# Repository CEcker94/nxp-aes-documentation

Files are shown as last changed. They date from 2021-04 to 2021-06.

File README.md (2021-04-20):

# NXP-AES-Documentation (nxp-aes-documentation)
The documentation for a Project of three Master Engineering-Students at the university of applied sciences in Landshut Germany (Ambrosch Markus, Summer Matthias and Ecker Christian).

This repository contains all the datasheets, pictures, circuit diagrams and most importantly the report of this project.

### 1.1 Information
The goal of the project is the construction and programming of a model vehicle for the Next Experience (NXP) Cup with a specially built, self-driving vehicle. In this competition the 1:18 scale vehicles must drive safely and independently through a course in the shortest possible time. The roadway is bordered by two black stripes applied to a white background. The vehicle must recognize these limitations and, based on their evaluation, adjust the speed of the vehicle and its steering angle.

### 1.2 Project
For the Project [>click-here<](https://github.com/CEcker94/nxp-aes-proj) 

The project contains the c-code for the autonomous driving vehicle.

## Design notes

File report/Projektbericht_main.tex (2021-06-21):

%*********************************************************************
%*************************** Main Document ***************************
%*********************************************************************

% Header includes document class and packages
\input{header/header}

\begin{document}

\pagenumbering{Alph} % Intern werden die Ersten seiten mit Alpha-Stiel nummeriert um Doppelreferenzen zu vermeiden 

% Titlepage
\input{titlepage/titlepage}
%%FERTIG

% Set page counter to 2 and page numbering to Roman
\pagenumbering{Roman}
\setcounter{page}{2}

% Section 0 Vorwort und Projektlinks
\input{sec0/sec0}
%%FERTIG

% Table of contents
\input{inserts/toc/toc}

% Table of acronyms
\input{inserts/acronym/acronym}

% Saving page counter value for attachement
\newcounter{pagecountersaving}
\setcounter{pagecountersaving}{\value{page}}

% Set page counter to 1 and page numbering to arabic
\pagenumbering{arabic}
\setcounter{page}{1}

% Section 1 Einführung
\input{sec1/sec1}
%FERTIG

% Section 2 Aufbau des Fahrzeugs
\input{sec2/sec2}
%FERTIG

% Section 3 Controllerplatine und Programmiertool
\input{sec3/sec3}
%FERTIG

% Section 4 Antrieb des Fahrzeugs
\input{sec4/sec4}
%FERTIG

% Section 5 Lenkung des Fahrzeugs
\input{sec5/sec5}
%FERTIG

% Section 6 Bedienungs-Board
\input{sec6/sec6}
%%FERTIG

% Section 7 Streckenerkennung des Fahrzeugs
\input{sec7/sec7}
%%FERTIG

% Section 8 Verteilerplatine
\input{sec8/sec8}
%%FERTIG

% Section 9 Regelung
%\input{sec9/sec9}

% Section 10 Inbetriebnahme des Fahrzeugs
%\input{sec10/sec10}

% Section 11 Zusammenfassung, Fazit und Ausblick
\input{sec11/sec11}
%--------------------------------------------------------------------Kapitel muss noch geschrieben werden

\pagenumbering{Roman}
\setcounter{page} {\thepagecountersaving}

% Table of graphics
\input{inserts/graphics/graphics}
%%FERTIG

% Table of sources
\input{inserts/sources/sources}
%%FERTIG

% Attachements
\input{attachement/attachement}
%---------------------------------------------------------------------Schaltplan einfügen
%---------------------------------------------------------------------Verweise auf Anhang in Text nicht vergessen!

\end{document}

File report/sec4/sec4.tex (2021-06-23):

%*****************************************************************
%*************************** Section 4 ***************************
%********************* Antrieb des Fahrzeugs *********************
%*****************************************************************

\pagestyle{fancy}
\rhead{\thepage} \chead{} \lhead{\ref{Sec4}. \nameref{Sec4}}
\cfoot{}

\section{Antrieb des Fahrzeugs}\label{Sec4}

Wie in Kapitel \ref{Sec2Sub1} beschrieben, wird das Fahrzeug von zwei \acp{BLDCMot} angetrieben, die im Folgenden genauer erklärt werden. Zusätzlich dazu wird in diesem Kapitel auch näher auf die Montage der Antriebskomponenten, die Programmierung des Antriebsbausteins, die Konfiguration der Motorcontroller und die Drehzahlmessung eingegangen.

\subsection{BLDC-Antrieb und Motorcontroller}\label{Sec4Sub1}

\acp{BLDCMot} sind im Wesentlichen wie permanent erregte Synchronmaschinen aufgebaut. Sie besitzen Magnete im Rotor und Einzelzahnwicklungen im Stator. Da solche Motoren häufig im \ac{RC}-Bereich Einsatz finden, gibt es zu deren Ansteuerung bereits vorgefertigte Bausteine, sogenannte \ac{ESC}. Diese haben zwei Signalpins für ein \ac{PWM}-Signal und zwei Anschlüsse zur Spannungsversorgung des Motorcontrollers, aus welchen die drei Strangspannungen für die Phasen des Antriebs generiert werden. Aus diesen Strangspannungen kann im übrigen auch die Motordrehzahl ermittelt werden, was im Rahmen dieser Projektarbeit auch eines der Ziele darstellt. An den Signalpins wird ein \ac{PWM}-Signal mit einer Frequenz von 50Hz angelegt, dessen Pulsbreite zwischen 1ms und 2ms liegen darf. Daraus resultiert ein Tastgrad zwischen 5\% (Stillstand) und 10\% (maximal erreichbare Drehzahl). Die maximale Drehzahl des Antriebs hängt von der Spannung des Akkus ab. Je geringer diese Spannung ist, desto geringer ist die maximal erreichbare Drehzahl. Der Anschluss der Motoren erfolgt nach der in Abbildung \ref{fig:SkizzeAntrieb} gezeigten Weise.

\begin{figure}[H] %H für Positionierung hier
 
\centering
\captionsetup{width=.95\textwidth}
\caption[Skizze zur Beschaltung eines \ac{ESC}s und \ac{BLDCMot}s]{Skizze zur Beschaltung eines \ac{ESC}s und \ac{BLDCMot}s; Versorgungsspannung des \ac{ESC}s in rot und schwarz (Masse), \ac{PWM}-Signalleitungen in grau und schwarz (Masse) und Anschlussleitungen des \ac{BLDCMot}s in rot, gelb und schwarz}\centering
\label{fig:SkizzeAntrieb}
\end{figure}

\subsection{Montage der Antriebskomponenten}\label{Sec4Sub2}

Die Komponenten des Fahrzeugantriebs, welcher über zwei \acp{BLDCMot} realisiert ist, sind auf der unteren Fahrzeugebene montiert. Die Motoren selbst sind mit zwei Schrauben an der Karosserie befestigt. An der Welle der Motoren befindet sich je ein Zahnrad mit 13 Zähnen, welches ein weiteres Zahnrad mit 90 Zähnen antreibt, das an der Antriebswelle befestigt ist. Das heißt, dass sich die Reifen bei 6,923 Umdrehungen der Motorwelle genau einmal drehen.\vspace{11pt}

In Abbildung \ref{fig:MontageMotorUebersetzung} sind die montierten Komponenten des linken Antriebs abgebildet. Die Befestigungsschrauben der Motoren sind dabei in rot hervorgehoben, die Befestigungsschrauben des Zahnrads der Antriebswelle in blau und die Befestigung des Reifens in orange. Das Zahnrad der Motorwelle ist durch Erhitzen geweitet und auf die Welle aufgesetzt worden. Zur Sicherheit dient hier etwas Sekundenkleber dazu, dass sich das Zahnrad auf der Welle nicht durchdreht. Sekundenkleber ist hier völlig ausreichend, da aufgrund der Übersetzung nur 1/7 des auf die Reifen wirkenden Moments auf das Zahnrad der Motorwelle wirkt.

\begin{figure}[H] %H für Positionierung hier
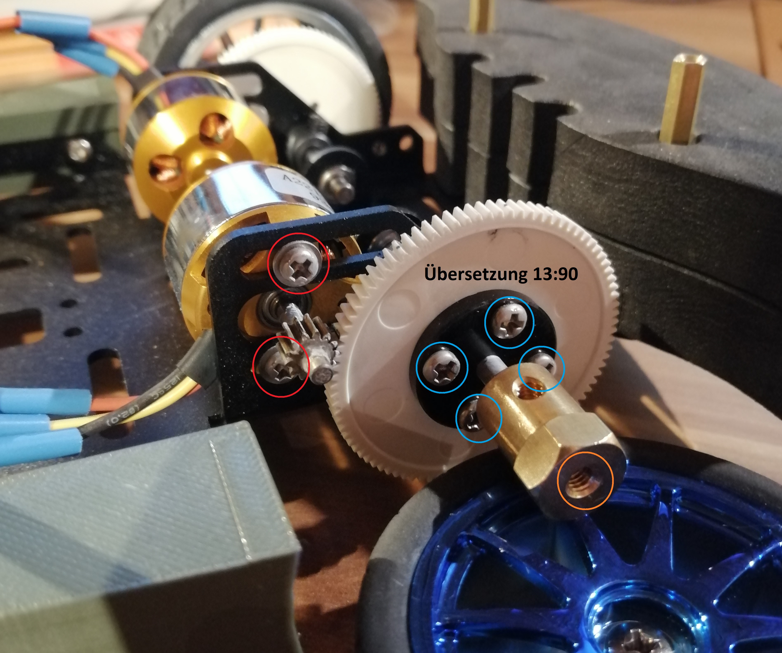
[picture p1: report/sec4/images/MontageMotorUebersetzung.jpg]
 
\centering
\captionsetup{width=.95\textwidth}
\caption[Montage der Antriebskomponenten]{Montage der \acp{BLDCMot} und Übersetzung auf die Antriebsachse; In rot die Befestigung des \ac{BLDCMot}s, in blau die Befestigung des Zahnrads an der Antriebswelle und in orange die Befestigung des Reifens}\centering
\label{fig:MontageMotorUebersetzung}
\end{figure}

\subsection{Konfiguration der Motorcontroller}\label{Sec4Sub3}

Die beiden Motorcontroller erwarten nach dem Zuschalten der Spannungsversorgung eine Initialisierungssequenz. Das Power-On-Ereignis wird vom \ac{ESC} mit drei Tönen (tief, mittel, hoch) signalisiert. Im Anschluss daran soll der Wert an der Signalleitung größer als 0\% sein. Das bedeutet, dass ein \ac{PWM}-Signal angelegt werden muss, welches eine Drehzahl N $\geq$ 0rpm repräsentiert. Der \ac{ESC} quittiert das Erkennen des \ac{PWM}-Signals mit einem tiefen Ton. Die Initialisierungssequenz ist allerdings erst dann beendet, wenn das \ac{PWM}-Signal an der Signalleitung zuerst vergrößert und dann auf 0\% verringert wird (N = 0rpm). Dabei gibt der \ac{ESC} einen letzten, hohen Ton von sich. Der Ablauf der Initialisierungssequenz ist in Abbildung \ref{fig:initESC} dargestellt. Nach dem letzten Ton ist die Initialisierung beendet und der \ac{BLDCMot} dreht sich in Abhängigkeit des an der Signalleitung anliegenden \ac{PWM}-Signals. 

\begin{figure}[H] %H für Positionierung hier
 
\centering
\captionsetup{width=.95\textwidth}
\caption[Initialisierungssequenz der \ac{ESC}s]{Initialisierungssequenz der \ac{ESC}s; Wert an der Signalleitung für die Initialisierungssequenz über der Zeit; 0\% entspricht dem \ac{PWM}-Tastgrad für den Stillstand und 100\% dem für die maximal erreichbare Drehzahl}\centering
\label{fig:initESC}
\end{figure}

Da die \ac{ESC}s individuell konfiguriert werden können und in der Dokumentation zu wenige Angaben gemacht werden, ist der Tastgrad für die Werte 0\% (Stillstand) und 100\% (maximal erreichbare Drehzahl) unbekannt. Deshalb ist es nicht möglich zu wissen, welche \ac{PWM}-Tastgrade für die Initialisierungssequenz verwendet werden müssen. Über die Konfiguration der \ac{ESC}s können die Grenzen für 0\% und 100\% selbst festgelegt werden. Für das Flashen der Motorcontroller wird die Software \glqq{}BLHeliSuite\grqq{} verwendet. Die Verbindung zwischen den \ac{ESC}s und der Software stellt ein Arduino Nano her.\vspace{11pt}

Der Arduino Nano muss zuvor mit einer neuen Software beschrieben werden. Um die \ac{ESC}s flashen zu können wird der Signalpin des zu programmierenden \ac{ESC} mit dem Pin D3 und der Massepin der Signalleitung mit einem Massepin des Arduino Nano verbunden. Danach wird in der Software \glqq{}BLHeliSuite\grqq{} im Reiter \glqq{}Make Interface\grqq{} eine neue Schnittstelle erstellt (siehe Abbildung \ref{fig:ConfigBLHeliSuite}). Auf der rechten Seite des Programm-Fensters wird ein Arduino Nano als Schnittstelle eingerichtet. Mit einem Klick auf den Button \glqq{}Arduino 4way-interface\grqq{} wird die neue Software, durch die die \ac{ESC}s neu konfiguriert werden können, auf den Arduino Nano geladen.

\begin{figure}[H] %H für Positionierung hier
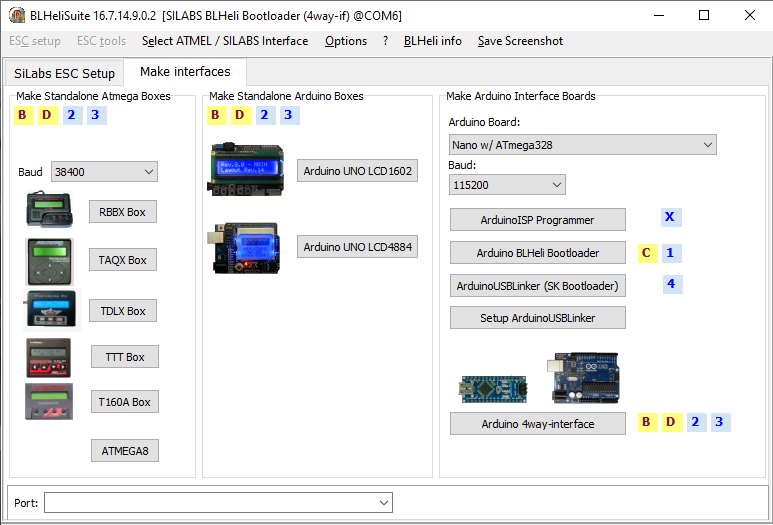
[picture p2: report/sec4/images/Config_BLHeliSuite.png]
 
\centering
\captionsetup{width=.95\textwidth}
\caption[Programmierung des Arduino Nano zur \ac{ESC}-Konfiguration]{Programmierung des Arduino Nano zur \ac{ESC}-Konfiguration mit der Software BLHeliSuite}\centering
\label{fig:ConfigBLHeliSuite}
\end{figure}

Nach dem Programmieren des Arduino Nano wird die Kommunikation der BLHeliSuite-Software mit dem \ac{ESC} hergestellt. Über die Schaltfläche \glqq{}Read Setup\grqq{} werden die voreingestellten Parameter des \ac{ESC} ausgelesen. Im nächsten Schritt werden die Zeiten für die Werte \glqq{}PPM min Throttle\grqq{} (0\% Aussteuergrad) und \glqq{}PPM max Throttle\grqq{} (100\% Aussteuergrad) auf 1100µs und 1900µs angepasst. Alle vorgenommenen Einstellungen sind in Abbildung \ref{fig:BLHeliSuite} einsehbar. Die Werte werden über die Betätigung der Schaltfläche \glqq{}Write Setup\grqq{} auf den \ac{ESC} geladen. Da jetzt die Werte für 0\% und 100\% Aussteuerung bekannt sind, können die einzelnen Schritte der Initialisierung im Programm des Fahrzeugs abgearbeitet werden.

\begin{figure}[H] %H für Positionierung hier
 
\centering
\captionsetup{width=.95\textwidth}
\caption[Parameter der neuen \ac{ESC}-Konfiguration]{Konfiguration der \ac{ESC}s mit der Software \glqq{}BLHeliSuite\grqq{}}\centering
\label{fig:BLHeliSuite}
\end{figure}

\subsection{Programmierung des Antriebsbausteins}\label{Sec4Sub4}

Der Antriebsbaustein der Software ist in zwei Dateien unterteilt, die Dateien \glqq{}drive.c\grqq{} und \glqq{}drive.h\grqq{}. Die Datei \glqq{}drive.h\grqq{} enthält alle relevanten Bibliotheken und Prototypen für die Datei \glqq{}drive.c\grqq{}.\vspace{11pt}

Außer der Einbindung der Bibliotheken und der Prototypen der Funktionen aus der Datei \glqq{}drive.c\grqq{} sind hier auch die Parameter für die Initialisierungssequenz der \ac{ESC}s und für die Initialisierung des Timers für die \ac{PWM}-Signale hinterlegt (Abbildung \ref{fig:DriveH}). 

\begin{figure}[H] %H für Positionierung hier
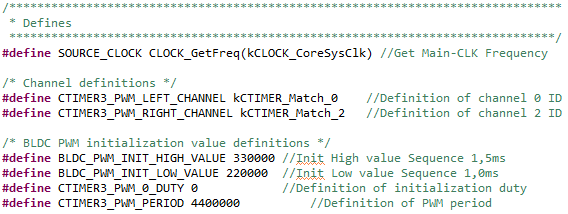
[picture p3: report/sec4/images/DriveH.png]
 
\centering
\captionsetup{width=.95\textwidth}
\caption[Relevante Zeilen der Datei \glqq{}drive.h\grqq{}]{Relevante Zeilen der Datei \glqq{}drive.h\grqq{} mit den Parametern für die Initialisierungssequenz der \ac{ESC}s und für die Initialisierung des \ac{PWM}-Timers}\centering
\label{fig:DriveH}
\end{figure}

Für die \ac{PWM}-Periodendauer wird bei der Initialisierung ein Wert von 4.400.000 Takten festgesetzt, woraus mit einer \ac{CPU}-Taktfrequenz von 220MHz (220.000.000 Takte pro Sekunde) eine Periodendauer von 20ms resultiert. Die Pulsbreite wird während des Programmablaufs regelmäßig überschrieben.\vspace{11pt}

Der \ac{ESC}-Initialisierungswert für den Stillstand (\glqq{}BLDC\_PWM\_INIT\_LOW\_VALUE\grqq{}, 220.000) entspricht hier einer \ac{PWM}-Pulsbreite von 1,0ms und der Initialisierungswert für die in etwa mittlere Aussteuerung (\glqq{}BLDC\_PWM\_INIT\_HIGH\_VALUE\grqq{}, 330.000) einer Breite von 1,5ms. Die volle Aussteuerung der Motoren wird, wie über die \glqq{}BLHeliSuite\grqq{} festgelegt, bei einer Pulsdauer von 1,9ms erreicht (BLDCMaxValue 1900µs, ca. 418.000). Eine Drehzahl von N = 0rpm wird theoretisch über die bei der \ac{ESC}-Konfiguration festgelegten 1,1ms ermöglicht (242.000). Da das \ac{PWM}-Signal leicht abweicht, wird ein etwas geringerer Wert veranlagt (BLDCMinValue 1090µs, ca. 240.000). Damit wird sichergestellt, dass sich die Räder im Stillstand nicht drehen.\vspace{11pt}

Die Parameter BLDCMaxValue und BLDCMinValue existieren im Code für die linke und rechte Antriebsseite separat (\glqq{}BLDCLeftMaxValue\grqq{}, \glqq{}BLDCLeftMinValue\grqq{} \& \glqq{}BLDCRightMaxValue\grqq{}, \glqq{}BLDCRightMinValue\grqq{}). Die Werte dieser Parameter kommen direkt aus dem \ac{EEPROM} und können mit dem Bedienungsboard eingestellt werden (siehe Abbildung \ref{fig:DriveC0}).\vspace{11pt}

\begin{figure}[H] %H für Positionierung hier
 
\centering
\captionsetup{width=.95\textwidth}
\caption[Extremwerte der Antriebsgeschwindigkeit als Parameter aus dem \ac{EEPROM}]{Extremwerte der Antriebsgeschwindigkeit als Parameter aus dem \ac{EEPROM}, deren Werte über das Bedienungsboard individuell einstellbar sind; Teil der Datei \glqq{}drive.c\grqq{}}\centering
\label{fig:DriveC0}
\end{figure}

\begin{figure}[H] %H für Positionierung hier
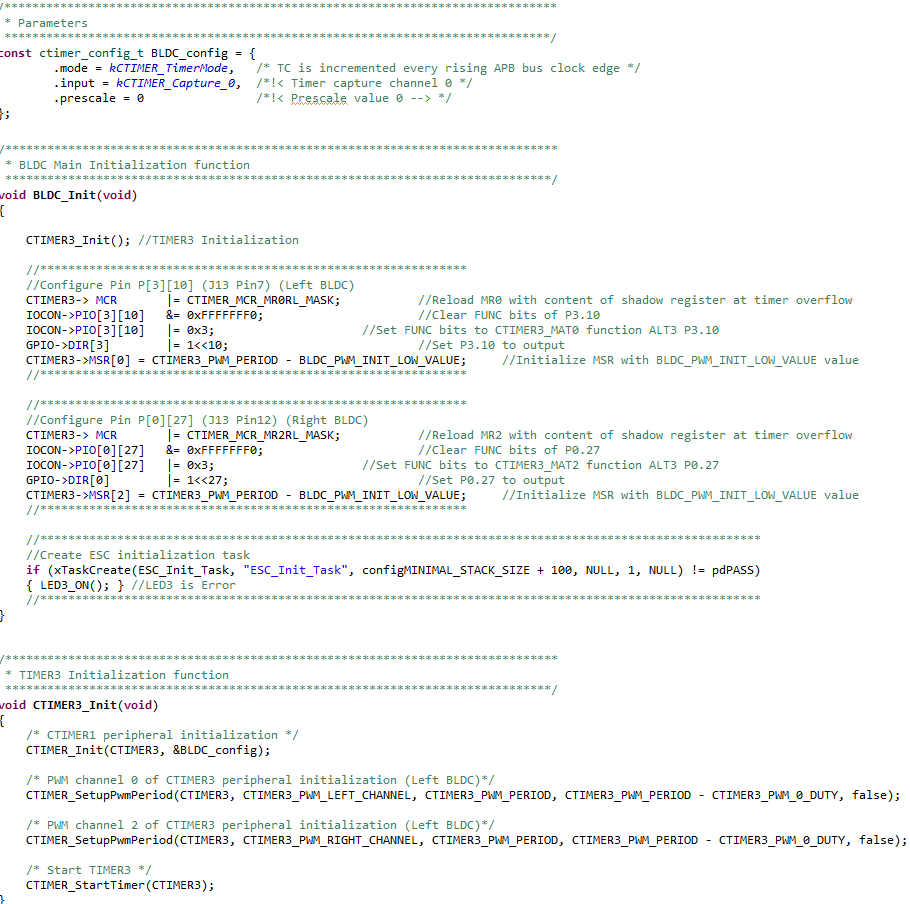
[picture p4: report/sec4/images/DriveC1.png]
 
\centering
\captionsetup{width=.95\textwidth}
\caption[Funktionen BLDC\_Init und CTIMER3\_Init der Datei \glqq{}drive.c\grqq{}]{Funktionen BLDC\_Init und CTIMER3\_Init der Datei \glqq{}drive.c\grqq{}}\centering
\label{fig:DriveC1}
\end{figure}

Auch die beiden \ac{PWM}-Timer (einer je Motorcontroller) benötigen bei der Initialisierung einige Parameter, deren Werte in der Datei \glqq{}drive.h\grqq{} festgelegt sind (PWM-Periodendauer, \ac{PWM}-Pulsdauer, Kanäle). Die Kanäle werden auf das Timer Match Register 2 (rechter Antrieb, \glqq{}kCTIMER\_Match\_2\grqq{}) und auf das Timer Match Register 0 (linker Antrieb, \glqq{}kCTIMER\_Match\_0\grqq{}) festgelegt, was bei dem verwendeten Controller den Pins P0.27 (rechts) und P3.10 (links) entspricht. Der Pin P3.10 wird auf der Controllerplatine über den Pin 7 und der Pin P0.27 über den Pin 12 der Buchsenleiste J13 nach außen geführt. Der Anschluss der Motorcontroller ist über den Anhang \glqq{}\nameref{SecAtt1}\grqq{} nachvollziehbar.\vspace{11pt}

Die Datei \glqq{}drive.c\grqq{} enthält die Funktionen zur Initialisierung der für die Verwendung der Antriebe notwendigen Controller-Peripherie (siehe Abbildung \ref{fig:DriveC1}) und zur Initialisierung der Motorcontroller (siehe Abbildung \ref{fig:DriveC2}).\vspace{11pt}

In der Funktion BLDC\_Init wird zuerst die Funktion CTIMER3\_Init aufgerufen, welche die beiden vorher festgelegten Kanäle des Timers C3 (\glqq{}kCTIMER\_Match\_0\grqq{} und \glqq{}kCTIMER\_Match\_2\grqq{}) mit den in der Datei ''drive.h'' festgelegten Parametern als \ac{PWM}-Timer mit einer Periodendauer von 20ms und einer Pulsdauer von 0ms initialisiert. Im Anschluss daran wird einzeln für beide Kanäle festgelegt, dass bei einem Timer-Überlauf die neuen Daten für die Pulslängen aus den Shadow-Registern geladen werden sollen. Zum Ändern der Geschwindigkeit eines der beiden Antriebe muss deshalb lediglich ein neuer Wert in das Shadow-Register geschrieben werden. Hier muss allerdings aufgepasst werden, da das Register nicht die Pulsbreite (On-Time) sondern die Off-Time erwartet. Deshalb muss der Wert, der eingetragen wird, der Periodendauer abzüglich der Pulsdauer entsprechen. Zusätzlich werden in der Funktion BLDC\_Init auch die Pins P3.10 und P0.27 für die Verwendung als \ac{PWM}-Ausgang des Timers C konfiguriert. Am Ende wird noch der erste \ac{ESC}-Initialisierungswert in die beiden Shadow-Register geschrieben, bevor die \ac{ESC}-Initialisierungsfunktion aufgerufen wird (siehe Abbildung \ref{fig:DriveC2}).\vspace{11pt}

Der Task BLDC\_Init\_Task beginnt mit dem Befüllen der Shadow-Register mit dem ersten Initialisierungswert. Nach einer Wartezeit von 2s wird der zweite Initialisierungswert in die Register geschrieben. Ebenfalls nach einer Zeit von 2s wird dann wieder der erste Initialisierungswert in die Shadow-Register geschrieben und die Initialisierung der \ac{ESC}s ist abgeschlossen. Die Wartezeiten sind notwendig, damit die \ac{ESC}s Zeit haben, die Änderungen zu erfassen.

\begin{figure}[H] %H für Positionierung hier
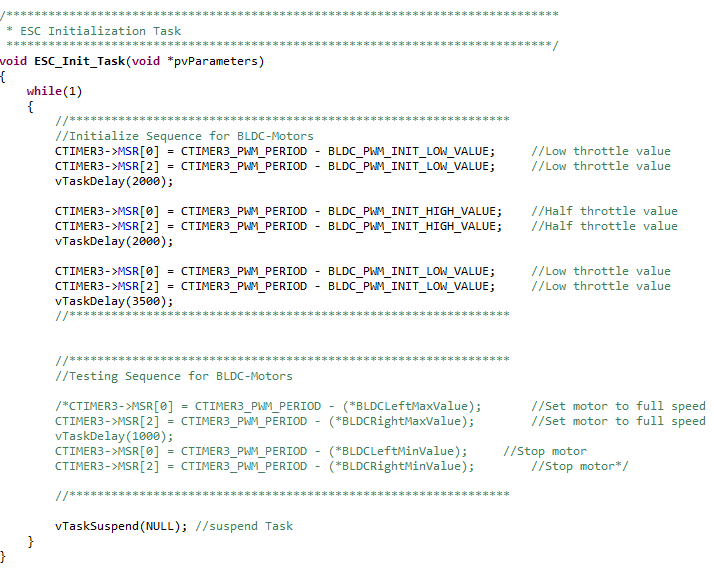
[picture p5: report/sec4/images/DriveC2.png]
 
\centering
\captionsetup{width=.95\textwidth}
\caption[Funktion BLDC\_Init\_Task der Datei \glqq{}drive.c\grqq{}]{Funktion BLDC\_Init\_Task der Datei \glqq{}drive.c\grqq{} zum Durchlaufen der Initialisierungssequenz der \ac{ESC}s}\centering
\label{fig:DriveC2}
\end{figure}

\newpage
\subsection{Drehzahlmessung}\label{Sec4Sub5}

Im folgenden Abschnitt zur Drehzahlmessung werden deren Notwendigkeit sowie Entwicklungsschritte und Realisierung erarbeitet. Des weiteren wird auch ein Ausblick für die Weiterentwicklung Schaltung gegeben.

\subsubsection{Erörterung der Notwendigkeit einer Drehzahlmessung}\label{Sec:NotwendigkeitDrehzahlmessung}

Die Quellspannung von Akkus verringert sich mit steigender Betriebszeit, weshalb bereits bei vorherigen Fahrzeug-Versionen eine Drehzahlmessung benötigt wird, um über eine Regelung die Spannungsabhängigkeit der Drehzahl bei \acp{DCMot} ausgleichen zu können. Die Spannungsabhängigkeit von \acp{DCMot} bereitet insbesondere beim Überfahren eines Hügels Probleme. Da die in den vorangegangenen Fahrzeugmodellen verwendeten \acp{DCMot} durch \acp{BLDCMot} ersetzt werden, stellt sich allerdings erneut die Frage nach der Notwendigkeit einer Drehzahlmessung. Die Variation der Drehzahl erfolgt bei \acp{DCMot} über die Änderung der Betriebsspannung, was auch die Abhängigkeit von der Versorgungsspannung erklärt. Die Drehzahlvariation bei einem \ac{BLDCMot} wird hingegen über eine Frequenzänderung der Strangspannungen realisiert. Zur Klärung der Frage nach einer Spannungsabhängigkeit der \acp{BLDCMot}, ist eine Messung am Prüfstand erforderlich.

\begin{figure}[H] %H für Positionierung hier
 
\centering
\captionsetup{width=.95\textwidth}
\caption[Messaufbau zur Prüfung der Spannungsabhängigkeit der \acp{BLDCMot}]{Messaufbau zur Prüfung der Spannungsabhängigkeit der \acp{BLDCMot}; in blau die Befestigung des Hecks an der Grundplatte des Prüfstands, in gelb die Befestigung der Vorderreifen am Prüfstand, in rot die DC-Motoren zur Spannungsmessung}\centering
\label{fig:Pruefstand01}
\end{figure}

Für die Durchführung der Messung wird ein bereits vorhandener Prüfstand für Modellfahrzeuge verwendet (siehe Abbildung \ref{fig:Pruefstand01}), welcher im Rahmen einer Bachelor-Abschlussarbeit an der HAW Landshut erstellt worden ist. Damit das Fahrzeug möglichst stabil auf dem Prüfstand steht und die Räder des Fahrzeugs ihre Rotationsbewegung besser auf die \acp{DCMot} des Prüfstands übertragen können, wird das Heck des Fahrzeugs mit Hilfe eines Drahtes am Prüfstand befestigt (Abbildung \ref{fig:Pruefstand01} blaue Markierung). Die vorderen Räder des Fahrzeuges sind ebenfalls am Prüfstand fixiert (Abbildung 44 gelbe Markierungen). \vspace{11pt}

Zur Überprüfung einer eventuellen Abhängigkeit der Drehzahl von der Versorgungsspannung, wird die Spannung an den vorhandenen \acp{DCMot} des Prüfstands gemessen, da diese direkt proportional zur Drehzahl ist (siehe Gleichung \ref{eq4.1}). Die Abhängigkeit der gemessenen Spannung von der Drehzahl ist allerdings nur annähernd linear, da die Drehmomentkonstante k\textsubscript{i} bei hohen Drehzahlen leicht einbricht. Aufgrund der für die Messung konstant eingestellten Pulsbreite von 1,5ms, spielt der Einbruch der Drehmomentkonstante allerdings keine große Rolle, da sich die Drehzahl, wenn überhaupt, nur sehr gering ändert. Dieser Zusammenhang kann deshalb vereinfachend als linear angenommen werden.\vspace{11pt}

Die Versorgungsspannung der \acp{ESC} wird für die Aufnahme verschiedener Messwerte zwischen 6,1V und 8V variiert. Ändert sich die gemessene Spannung mit der Variation der Versorgungsspannung, so ist das ein hinreichender Beweis dafür, dass die Drehzahl der \acp{BLDCMot} spannungsabhängig ist. Die Ergebnisse der Messreihe aus Tabelle \ref{tab:PruefstandMess01} sind zur einfacheren Auswertung in Abbildung \ref{fig:Pruefstand02} visualisiert.

\begin{equation}\label{eq4.1}
U_A = k_i \cdot N \cdot \frac{\pi}{30}
\end{equation}

\begin{table}[H]
\begin{tabular}{|c|c|c|c|c|c|c|c|c|c|c|}
\hline
\rule{0pt}{15pt} Messung & 1&2&3&4&5&6&7&8&9&10 \\
\hline
U\textsubscript{Versorgung} [$V$]&8.0&7.9&7.8&7.7&7.6&7.5&7.4&7.3&7.2&7.1 \\ 
\hline
U\textsubscript{Messung} [$V$]&5.80&5.75&5.65&5.57&5.48&5.40&5.35&5.25&5.18&5.09 \\
\hline
\hline
\rule{0pt}{15pt} Messung & 11&12&13&14&15&16&17&18&19&20 \\
\hline
U\textsubscript{Versorgung} [$V$]&7.0&6.9&6.8&6.7&6.6&6.5&6.4&6.3&6.2&6.1 \\ 
\hline
U\textsubscript{Messung} [$V$]&5.05&4.96&4.87&4.82&4.69&4.73&4.66&4.60&4.50&4.45 \\
\hline
\end{tabular}
\centering
\captionsetup{width=.95\textwidth}
\caption[Messreihe 1: Spannungsabhängigkeit Drehzahl]{Messreihe 1: Messwerte für Überprüfung einer eventuellen Spannungsabhängigkeit der Drehzahl}\centering
\label{tab:PruefstandMess01}
\end{table}

Aus Abbildung \ref{fig:Pruefstand02} kann die Erkenntnis abgeleitet werden, dass die Drehzahl der \acp{BLDCMot}, welche proportional zu der an den \acp{DCMot} gemessenen Ankerspannung U\textsubscript{Messung} ist, bei einem Abfallen der Versorgungsspannung nicht konstant bleibt, denn andernfalls wäre die resultierende Gerade eine Horizontale. Deshalb ist die Drehzahl der \acp{BLDCMot} wie die der \acp{DCMot} abhängig von der Versorgungsspannung.\vspace{11pt}

Die sich aus der Messreihe ergebende Erkenntniss, führt zu dem Entschluss, dass eine Drehzahlregelung nicht nur sinnvoll, sondern auch erforderlich ist. Denn während der Durchfahrt des Parcours wird nicht zu jedem Zeitpunkt die volle Drehzahl benötigt. Folglich hat eine Regelung den Vorteil, dass die vorgegebene Drehzahl auch bei einer fortschreitenden Entladung des Akkus weiterhin aufrecht gehalten werden kann. Wird eine feste Geschwindigkeit vorgegeben, kann die Regelung bei fallender Versorgungsspannung der \acp{ESC} das \ac{PWM}-Signal bis zur Stellgrenze (Pulsbreite = 1,9ms) erhöhen. Erst bei Erreichen der Stellgrenze nimmt die Drehzahl linear mit der Versorgungsspannung ab.

\begin{figure}[H] %H für Positionierung hier
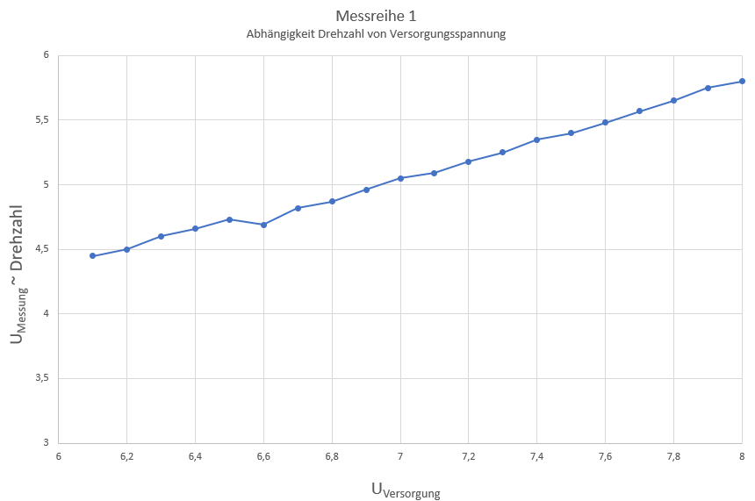
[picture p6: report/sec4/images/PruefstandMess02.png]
 
\centering
\captionsetup{width=.95\textwidth}
\caption [Spannungsabhängigkeit der Drehzahl von der Versorgungsspannung]{Spannungsabhängigkeit der Drehzahl der \acp{BLDCMot} von der Versorgungsspannung}\centering
\label{fig:Pruefstand02}
\end{figure}

Des weiteren muss das Fahrzeug im Rahmen des NXP-Cups nach dem Überfahren der Ziellinie innerhalb von zwei Metern anhalten können. In der Konfiguration der \acp{ESC} bietet sich dafür die Einstellung \glqq{}Break On Stop\grqq{} an, mit der das Fahrzeug bei einer PWM-Pulsdauer von 1,1ms (BLDCMinValues: BLDCLeftMinValue, BLDCRightMinValue) aktiv bremst, indem die drei Phasen der \acp{BLDCMot} auf Masse geschlossen werden.\vspace{11pt}

Zur Verifizierung eines ordnungsgemäßen Bremsverhaltens, wird eine Probefahrt auf einer langen geraden Strecke an der HAW Landshut durchgeführt. Die Antriebe sind dabei so konfiguriert das sich das Fahrzeug nach der Initialisierung der \acp{BLDCMot} unmittelbar mit maximaler Geschwindigkeit fortbewegt und nach kurzer Fahrtdauer (ca. 3s) stoppt (BLDCMinValues). Hierbei stellt man fest, dass die Bremskraft ausreicht, um das Fahrzeug innerhalb von ca. 30 cm zum Stehen zu bringen.\vspace{11pt}

Während des Testens fällt auf, dass sich die Reifen trotz gleicher ESC-Konfiguration unterschiedlich schnell drehen. Der Grund für dieses Problem lässt darauf schließen, dass die beiden Antriebsseiten einen unterschiedlichen Reibungswert aufweisen. Das kann daran liegen, dass bei den Achsen keine Lager verwendet werden und bei der Übersetzung das Getriebespiel (zwischen den Zahnrädern) auf beiden Antriebsseiten unterschiedlich groß ist, was ebenfalls die Reibung beeinflusst.\vspace{11pt}
%Zum anderen wird davon ausgegangen, dass bei minimalen und maximalen Antrieb die Stellgrenzen (1,09ms und 1,9ms) sprich die ON-Zeit des PWM-Signals kurzfristig über- bzw. unterschritten wird. Befindet sich die Pulsbreite außerhalb des konfigurierten Bereiches schaltet der Antrieb kurzweilig aufgrund des undefinierten Signalzustandes ab und bei Rückkher in den definierten Bereich wieder an.\vspace{11pt} 

Die Spannungsabhängigkeit der \acp{BLDCMot} sowie das unterschiedliche und reibungsabhängige Drehverhalten der beiden Antriebe, machen eine Drehzahlregelung zwingend erforderlich, um ein zuverlässiges und sicheres Fahrverhalten zu gewährleisten.

\subsubsection{Auswahl des Messprinzips}\label{Sec4Sub5Sub2}

Aufgrund der Erkenntnis, dass eine Drehzahlregelung der \acp{BLDCMot} erforderlich ist, gilt es in diesem Abschnitt entsprechende Messprinzipien zur Drehzahlerfassung gegenüberzustellen und die für dieses Projekt sinnvollste Messmethode zu bestimmen.\vspace{11pt}

Die in bisherigen Fahrzeugversionen am häufigsten verwendeten Methoden zur Drehzahlerfassung sind die Verwendung von Hallsensoren oder Lichtschranken (siehe Abbildung \ref{fig:Vorgaengerfahrzeug}). Hallsensoren und Lichtschranken eignen sich hervorragend für eine berührungslose Drehzahlerfassung. Für die Drehzahlmessung mithilfe von Hallsensoren werden kleine Magnete auf der Innenseite der Hinterräder angebracht, welche vom Hallsensor erfasst werden (Abbildung \ref{fig:Vorgaengerfahrzeug}, links). Anhand der Zeit zwischen den Zuständen \glqq{}Magnet vorhanden\grqq{} oder \glqq{}Magnet nicht vorhanden\grqq{} (HIGH/LOW-Signal), kann unter Berücksichtigung der jeweiligen Getriebeübersetzung und Menge der Magnete die Drehzahl der \acp{BLDCMot} bestimmt werden. Die Drehzahlmessung mit einer Lichtschranke funktioniert in der Auswertung genau wie die Messung mit  Hallsensoren, lediglich die Messmittel sind anders (Abbildung \ref{fig:Vorgaengerfahrzeug}, rechts).

\begin{figure}[H] %H für Positionierung hier
 
 
\captionsetup{width=.95\textwidth}
\centering
\caption[Varianten der Drehzahlerfassung bei vorherigen Fahrzeugversionen]{Varianten der Drehzahlerfassung bei vorherigen Fahrzeugversionen; links: Hallsensoren; rechts: Lichtschranke}\centering
\label{fig:Vorgaengerfahrzeug}
\end{figure}     

Ein Hallsensor bietet den Vorteil, dass neben der Erfassung der Drehzahl auch die Drehrichtung mit Hilfe eines zweiten um 90° versetzten Hallsensors bestimmt werden kann. Dazu muss nicht einmal ein zweiter Sensor gekauft werden, da bereits zwei Hallsensoren in einem Gehäuse verbaut sind. Im Zuge dieser Projektarbeit ist eine Erfassung der Drehrichtung jedoch nicht erforderlich, da die für die \acp{BLDCMot} verwendeten \acp{ESC} so konfiguriert sind, dass nur eine Fahrt in Vorwärtsrichtung möglich ist. Ein weiterer Vorteil des Hallsensors aber auch einer Lichtschranke ist, dass die für die GPIO-Pins notwendigen Rechtecksignale direkt vorgegeben werden und keine zusätzliche Umformung des Signals mehr notwendig ist. \vspace{11pt}

Aufgrund der Klebebefestigung der Magnete besteht das Risiko, dass diese sich nach einer gewissen Zeit ablösen und somit die Daten zur Drehzahlerfassung verfälschen. Wie in Abbildung \ref{fig:Vorgaengerfahrzeug} zusätzlich zu erkennen ist, ist die Montage des Hallsensors, die lediglich über die Versorgungsdrähte oder eine zusätzliche Drahtstütze realisiert ist, sehr anfällig auf Erschütterungen. Eine zuverlässige und weniger erschütterungsempfindliche Montage des Hallsensors erfodert deshalb eine zusätzliche Halterung (3D-Druck Anbauteil). Diese Halterung muss erst konstruiert, gedruckt und montiert werden. Um mechanische Probleme, wie sie durch Erschütterungen entstehen können, vollständig zu eliminieren, bietet sich die Anwendung eines anderen, bisher noch nicht erwähnten Messprinzips an, auf welches in weiteren Verlauf genauer eingegangen wird.\vspace{11pt}

Die Alternativmethode zur Erfassung der Drehzahl ist die Anbindung eines Tiefpassfilters mit nachgeschaltetem Komparator an eine der \ac{BLDCMot}-Phasen. Die Schaltung filtert die hochfrequenten Anteile des Phasensignals heraus. Mithilfe einer Komparatorschaltung wird daraus ein Rechtecksignal mit steilen Flanken erzeugt. Hierbei wird das auf der Phase vom \ac{ESC} bereitgestellte, hochfrequente Signal (Abbildung \ref{fig:Signaldarstellung}, grüner Signalverlauf V(in)) abgegriffen. Durch die mit dem Schaltungssimulationstool LTSpice entwickelte und auf einer Lochrasterplatine in Hardware realisierte Tiefpass- und Komparatorschaltung kann dieses abgegriffene Signal in ein eindeutiges Rechtecksignal umgeformt werden (Abbildung \ref{fig:Signaldarstellung}, pinker Signalverlauf V(out)).\vspace{11pt}

Bei der Drehzahlmessung wird der zeitliche Abstand zwischen zwei aufeinanderfolgenden, steigenden Flanken des aus der Tiefpass-/Komparatorschaltung generierten Rechtecksignals mit Hilfe eines Timer-Zählers bestimmt. Die erfassten Zeiten zwischen den Flanken sind proportional zur Drehzahl und können direkt für die Drehzahlregelung verwendet werden, ohne die tatsächliche Drehzahl errechnen zu müssen.\vspace{11pt}

Es gilt zu erwähnen, dass auch bei dieser Methode eine Erfassung der Drehrichtung möglich wäre. Bei drei Phasen, welche um 120° zueinander versetzt sind, kann die Drehrichtung anhand der Pulsreihenfolge der einzelnen Phasen bestimmt werden, wobei nur zwei der drei Phasen benötigt werden. Aufgrund dessen, dass die ESCs lediglich eine feste Drehrichtung erlauben (harte Konfiguration), wird die Drehrichtungsbestimmung nicht benötigt.

\begin{figure}[H] %H für Positionierung hier
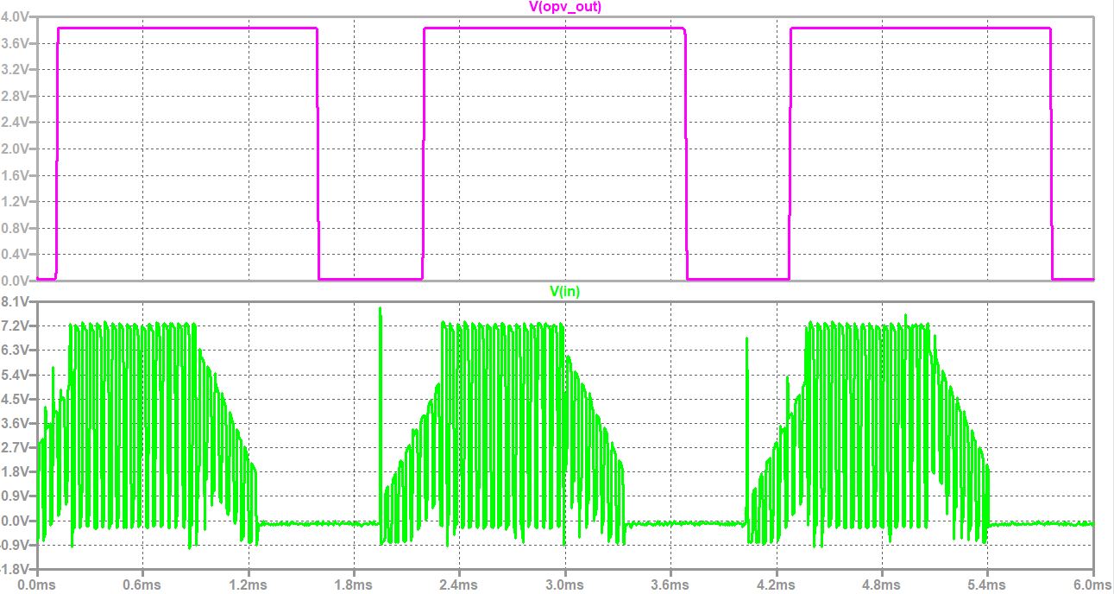
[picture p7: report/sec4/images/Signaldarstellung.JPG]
 
\centering
\captionsetup{width=.95\textwidth}
\caption[Phaseneingangssignal und Ausgangssignal der Tiefpass-/Komparatorschaltung]{Phasensignal eines Antriebs (V(in), grün) bei schneller Fahrt und Darstellung des simulierten Ausgangssignals (V(out), pink) aus der Tiefpass-/Komparatorschaltung; erstellt und simuliert mit dem Schaltungssimulationstool LTspice XVII}\centering
\label{fig:Signaldarstellung}
\end{figure}

Da auch bei diesem Messprinzip ein hoher Aufwand (Entwicklungs- und Simulationsaufwand) erforderlich ist, gilt es abzuwägen, welche dieser Methoden am vorteilhaftesten für das Gesamtprojekt ist. Unter Betrachtung der Vor- und Nachteile aller Messprinzipien bietet sich die Tiefpass-/Komparatorschaltung am meisten an. Insbesondere die Unempfindlichkeit gegen Erschütterungen und die Verwendung der ohnehin von den ESCs bereitgestellten Phasensignale, spricht für die Realisierung der Drehzahlmessung mit dieser Methode. Als weitere Gründe gegen die sonstigen Messprinzipien sprechen die unzuverlässige Montage von Hallsensoren oder Lichtschranken und die fehlende Notwendigkeit einer Erfassung der Drehrichtung.

\newpage

\subsubsection{Hardware für die Drehzahlmessung}\label{Sec4Sub5Sub3}

In diesem Abschnitt wird die Entwicklung der Schaltung zur Drehzahlmessung beschrieben. Dabei wird sowohl auf die Probleme eingegangen, die sich während der Schaltungsentwicklung ergeben als auch auf deren Behebung. Damit das Phasensignal in ein eindeutiges Rechtecksignalsignal umgesetzt werden kann, bedarf es der im vorherigen Abschnitt erörterten Entwicklung einer Tiefpass-/ Komparatorschaltung. Es soll deutlich gemacht werden, welche Bauteile verwendet werden und welchen Zweck diese in der Schaltung erfüllen. Zur Entwicklung und Simulation der Drehzahl-Messschaltung wird das Schaltungssimulationstool LTspice XVII und zur Erstellung des Platinenlayouts die Freeware BlackBoard Circuit Designer verwendet.\vspace{11pt}

Zu Beginn wird die Schaltung für ein Phasensignal in LTspice realisiert. Der daraus resultierende Schaltplan zur Drehzahlmessung ist in Abbildung \ref{fig:Schaltungsaufbau} sichtbar und dient als Überblick über die verwendeten Bauteile mit deren entsprechenden Kennwerten. Es gilt zu erwähnen, dass der Spannungsteiler (R5, R6, R7, R8) zwischen Vref und dem invertierenden Operationsverstärkereingang IN- nur einmal realisiert werden muss, worauf im weiteren noch detaillierter eingegangen wird.

\begin{figure}[H] %H für Positionierung hier
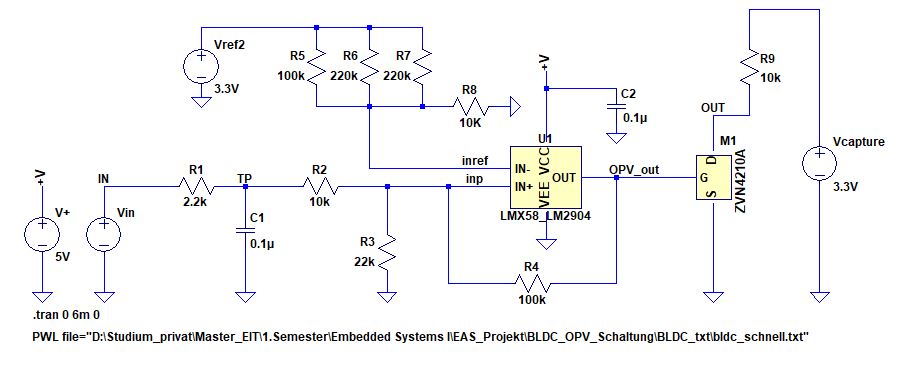
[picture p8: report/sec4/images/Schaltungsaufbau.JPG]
 
\centering
\captionsetup{width=.95\textwidth}
\caption[Schaltplan der Tiefpass-/Komparatorschaltung aus LTspice XVII]{Schaltplan der Tiefpass-/Komparatorschaltung; erstellt für die Simulation eines Phasensignals in LTspice XVII}\centering
\label{fig:Schaltungsaufbau}
\end{figure}

Das Phasensignal wird von der Spannungsquelle Vin repräsentiert. Die Signale werden vor der Schaltungsentwicklung zwischen einer Phase eines ESCs und dem Massepotential mit dem Oszilloskop gemessen. Hierzu werden die Antriebe auf den Modell-Prüfstand gestellt und je einmal mit hoher und geringer Drehzahl angesteuert. Es gilt zu erwähnen, dass die erfassten Signale für schnelle und langsame Fahrt nicht den maximalen und minimalen Drehzahlen entsprechen. Das Oszilloskop (DSO-X 3034A) bietet die Möglichkeit die gemessenen Ausgangssignale als .csv-Datei auf einem USB-Stick zu speichern. Das gespeicherte .csv-Datei wird daraufhin als \ac{PWLFile} importiert und einer Spannungsquelle übergeben (rechter Mausklick auf Spannungsquelle / PWL-File anwählen / Pfad .csv-Datei wählen). Bevor die .csv-Datei importiert werden kann, muss die Datei umformatiert werden.\vspace{11pt}

Das ungefilterte Phasensignal besitzt eine Frequenz von ca. 23 kHz. Um die hohen Frequenzanteile des Signals im ersten Schritt zu filtern, wird zunächst ein Tiefpass erster Ordnung benötigt. Die Dimensionierung des Tiefpasses erfolgt mit einem 2,2kOhm Widerstand (R1) und einem 100nF Kondensator (C1). Dabei beträgt die Grenzfrequenz f\textsubscript{G} des Tiefpasses nach Gleichung \ref{eq4.2} 723Hz. Der aus der Simulation resultierende Spannungsverlauf sowie der am Oszilloskop gemessene Spannungsverlauf nach der Tiefpassfilterung sind in den Abbildungen \ref{fig:SpannungsverlaufTPSpice} und \ref{fig:SpannungsverlaufTPReal} dargestellt (unterschiedliche Drehzahlen!).

\begin{equation}\label{eq4.2}
f_G = \frac{ 1 }{2 \cdot \pi \cdot R1\cdot C1 }
\end{equation}

\begin{figure}[H] %H für Positionierung hier
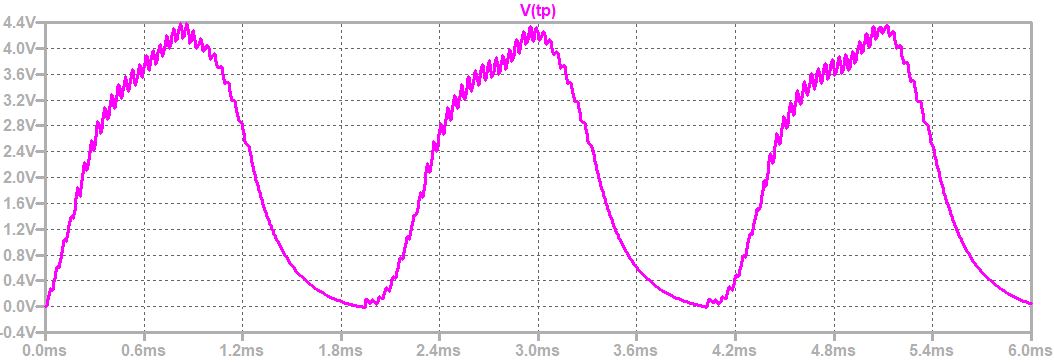
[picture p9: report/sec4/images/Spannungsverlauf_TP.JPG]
 
\centering
\captionsetup{width=.95\textwidth}
\caption[Simulationsergebnis des Phasensignals nach dessen Tiefpassfilterung]{Simulationsergebnis des Phasensignals nach dessen Tiefpassfilterung bei schneller Fahrt}\centering
\label{fig:SpannungsverlaufTPSpice}
\end{figure}

\begin{figure}[H] %H für Positionierung hier
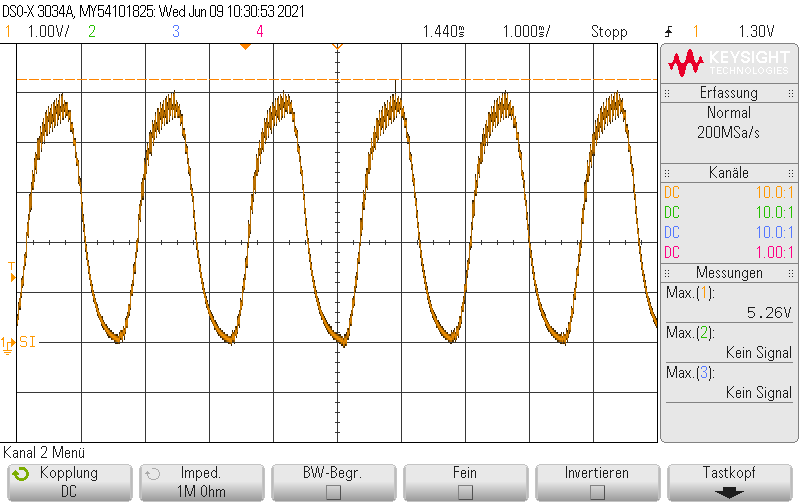
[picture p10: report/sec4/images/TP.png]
 
\centering
\captionsetup{width=.95\textwidth}
\caption[Messergebnis des Phasensignals nach dessen Tiefpassfilterung]{Messergebnis des Phasensignals nach dessen Tiefpassfilterung bei schneller Fahrt}\centering
\label{fig:SpannungsverlaufTPReal}
\end{figure}

Das zentrale Bauelement der Schaltung ist ein von \ac{TI} hergestellter Operationsverstärker LM358A, welcher als Komparator verwendet wird. Für eine maximal realistische Simulation wird ein Simulations-Modell des Herstellers in LTspice XVII eingebunden \cite{OPVModel}. Hierbei handelt sich um einen \ac{OPV}, welcher im Single-Supply betrieben wird. Der \ac{OPV} wird zunächst mit einer Versorgungsspannung V+ von 5V betrieben, welche wie die Versorgungsspannung des Controllers vom Linearspannungsregler abgegriffen wird. Für die Drehzahlmessung wird jeweils eine Schaltung für das Phasensignal des linken und rechten Antriebs benötigt. Der \ac{OPV} ermöglicht es, beide Signale in einem Bauteil zu verarbeiten. Dazu besitzt er zwei invertierende Eingänge (IN1-, IN2-) und zwei nicht-invertierende Eingänge (IN1+, IN2+) sowie zwei Ausgänge (OUT1, OUT2) (siehe Abbildung \ref{fig:OPVPinbelegung}). Dadurch kann auf der Verteilerplatine zusätzlicher Platz eingespart werden.

\begin{figure}[H] %H für Positionierung hier
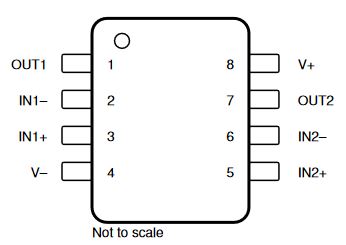
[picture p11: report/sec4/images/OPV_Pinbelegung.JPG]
 
\centering
\captionsetup{width=.95\textwidth}
\caption[Pinbelegung des Operationsverstärkers LM358A]{Pinbelegung des Operationsverstärkers LM358A}\centering
\label{fig:OPVPinbelegung}
\end{figure}

Da der \ac{OPV} in der Schaltung als Schmitt-Trigger verwendet wird, müssen einige schaltungstechnische Maßnahmen, wie z.B. ein Spannungsteiler mit Rückführwiderstand hinzugefügt werden. Die Realisierung des Spannungsteilers erfolgt mit den Widerständen R2 = 10kOhm, R3 = 22 kOhm sowie einem Rückführwiderstand R4 = 100kOhm.\vspace{11pt}

Grundsätzlich verstärkt ein \ac{OPV} ständig die Differenz seiner Eingangsgrößen (IN+, IN-). Da ein Operationsverstärker einen theoretisch unendlichen Verstärkungsfaktor besitzt, reicht eine geringe Eingangsspannungsdifferenz aus, um den Ausgang bei dieser Schmitt-Trigger Schaltung in die Versorgungsspannungsbegrenzung zu treiben (nur Werte bis V+). Der verwendete OPV LM358A besitzt einen \glqq{}open-loop voltage gain\grqq{} von 100V/mV. Die Hysterese wird durch den Rückkopplungsanteil (R4) der Ausgangsspannung des \ac{OPV} bestimmt. Aus dieser Art der Rückführung entsteht eine Schmitt-Triggerschaltung welche den Vorteil hat, dass sie unempfindlich gegen Schwankungen innerhalb des Hysteresebandes ist (Schwankungen wie z.B. Rauschen). So wird ein unregelmäßiges Schaltverhalten am \ac{OPV}-Ausgang verhindert und ein sauberes Ausgangssignal erzeugt (siehe Abbildung \ref{fig:inpInrefOpvOut}).\vspace{11pt}

Wie bereits erwähnt kann der Ausgang des OPV im Idealfall seine Versorgungsspannung V+ und V- annehmen. Da das verwendete OPV-Modell nicht über einen Rail-to-Rail Ausgang verfügt, bleibt die maximale Ausgangsspannung stets mit einem nicht zu vernachlässigbarem Abstand unter der Versorgungsspannung. Bei einer \ac{OPV}-Versorgungsspannung V+ von 3,3V werden am Ausgang des OPV ungefähr 2V gemessen. Dies führt dazu, dass das Phasensignal im unteren und oberen Drehzahlbereich die Referenzspannung Vref von 540mV am invertierenden Eingang des OPV nicht durchschreitet. Dadurch wird am OPV-Ausgang kein Rechtecksignal mehr erzeugt. Darüber hinaus ist im zugehörigen Datenblatt des verwendeten Mikrocontrollers ersichtlich, dass die Capture Input Pins vom Timer Modul CTIMER2 (J13 Pin4 / Port-Pin P0.25 für Messung rechts, J13 Pin6 / Port-Pin P0.24 Messung links) eine Mindestspannung von 2,0V benötigten, um zuverlässig einen HIGH-Pegel erkennen zu können. Da dieser Spannungswert insbesondere im niedrigen Drehzahlbereich nie erreicht wird, muss die Versorgungsspannung des OPV hochgesetzt werden. In Abbildung \ref{fig:inpInrefOpvOut} wird die Abweichung bei einer Versorgungsspannung von 5V deutlich. Das Ausgangssignal des Operationsverstärkers (Abbildung \ref{fig:inpInrefOpvOut}, gelb) erreicht einen Spannungspegel von 3.85V. Durch die Erhöhung der Versorgungsspannung kann also grundsätzlich eine höhere Ausgangsspannung erzielt werden.

\begin{figure}[H] %H für Positionierung hier
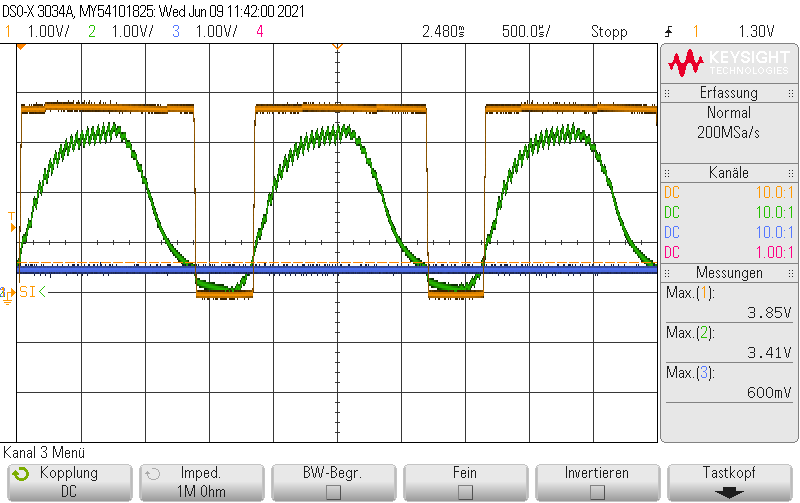
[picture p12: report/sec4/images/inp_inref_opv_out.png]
 
\centering
\captionsetup{width=.95\textwidth}
\caption[Beispielhafte Messung des OPV-Ausgangssignals bei V+ = 5,0V;]{Beispielhafte Messung des OPV-Ausgangssignals (gelb) bei einer Versorgungsspannung von V+ = 5,0V;  IN+ in grün und Vref an IN- in blau}\centering
\label{fig:inpInrefOpvOut}
\end{figure}

Damit eine Signalspannung mit mehr als 2,0 V für die Capture Input Pins des Timer Moduls CTIMER2 am Mikrocontroller zuverlässig bereit gestellt wird, wird ein n-Kanal MOSFET (ZVN4210A) an jedem der OPV-Ausgänge platziert. Der Widerstand R9 = 10 kOhm vor dem Drain-Anschluss des MOSFETs in Abbildung \ref{fig:Schaltungsaufbau} steht stellvertretend für den internen Pull-up Widerstand der TIMER2 Capture Input Pins des Mikrocontrollers. Je nach Konfiguration können diese zu- oder abgeschalten werden.\vspace{11pt}

Für die Bereitstellung der am invertierenden OPV-Eingang (IN-) benötigten Referenzspannung, auch Schwellspannung genannt, wird ein Spannungsteiler mit einer vom Pin12 der Buchsenleiste J10 stammenden +3,3V Spannungsversorgung vorgeschalten. Der Spannungsteiler besteht aus drei parallel geschaltenen Widerständen R5 = 100kOhm und R6 = R7 = 220kOhm in Reihe zum Widerstand R8 = 10kOhm. Die dadurch erzeugte Referenzspannung beträgt etwa 540mV. Diese Referenzspannung ist in der Theorie ausreichend, um für alle Drehzahlen ein zuverlässiges Rechtecksignal zu erzeugen. Trotz aller bisher getroffenen Optimierungen treten dennoch immer wieder Probleme bei der Drehzahlmessung auf. Die Problematik sowie deren Lösung werden im Kapitel \ref{Sec4Sub5Sub4} \nameref{Sec4Sub5Sub4} beschrieben.

\begin{figure}[H] %H für Positionierung hier
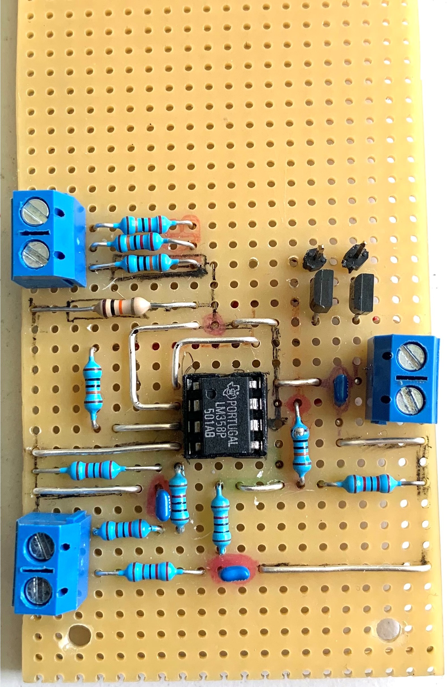
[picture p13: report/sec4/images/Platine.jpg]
 
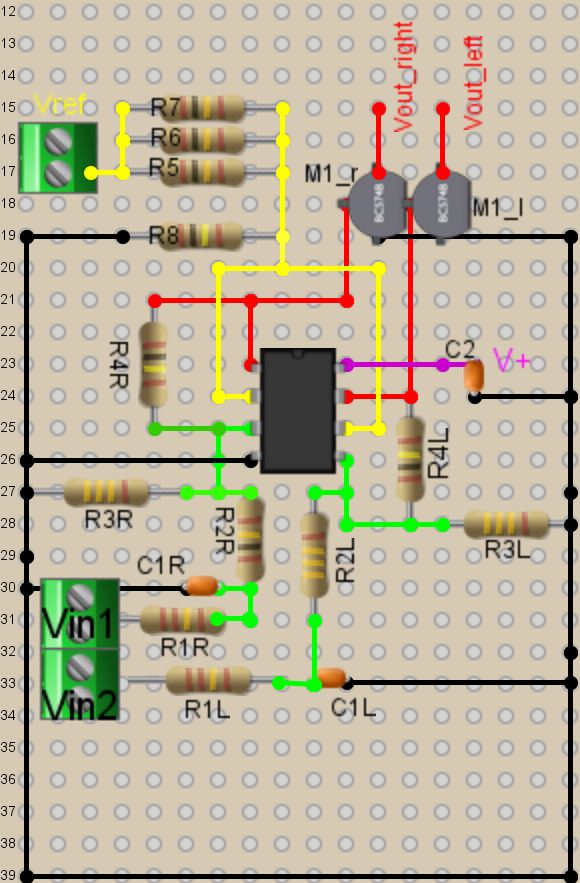
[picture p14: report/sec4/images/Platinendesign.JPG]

\captionsetup{width=.95\textwidth}
\centering
\caption[Schaltung der Drehzahlmessung und zugehöriges Layout] {Schaltung der Drehzahlmessung auf der Signalverteilerplatine (links) und zugehöriges Layout (rechts)}\centering
\label{fig:DrehzahlmessSignalvertPlat}
\end{figure}

Auf der linken Seite der Abbildung \ref{fig:DrehzahlmessSignalvertPlat} ist die auf der Signalverteilerplatine befindliche Drehzahl-Messschaltung im Original zu sehen. Auf der rechten Seite der Abbildung \ref{fig:DrehzahlmessSignalvertPlat} befindet sich das dafür mit dem Programm BlackBoard Circuit Designer erstellte, zugehörige Layout. Die grünen Verbindungen stellen die Pfade zwischen Vin (Phasensignale) und den OPV Eingängen IN1+ und IN2+ dar. Gelbe Linien repräsentieren den Pfad der Referenzspannung Vref zu den invertierenden Eingängen IN1- und IN2-. Der Pfad zur Spannungsversorgung des OPV (V+) ist in violett dargestellt und alle schwarzen Verbindungen stellen GND-Verbindungen dar. Zuletzt kann der Verlauf der Ausgangsspannungen vom OPV an die Capture Eingänge des Timers CTIMER2 anhand der roten Verbindungen nachvollzogen werden. 

\newpage
\subsubsection{Programmierung des Drehzahlmessungsbausteins}\label{Sec4Sub5Sub5}

Damit die durch die Schaltung bereitgestellten Rechtecksignale (links, rechts) vom Mikrocontroller erfasst werden können, werden die Capture Register des Timer-Moduls CTIMER2 verwendet. Dieses Modul löst bei einem Flanken-Ereignis (steigende Flanke) am jeweiligen Capture Input Pin einen Interrupt aus, in welchem die verstrichene Zeit seit der letzten steigenden Flanke errechnet wird und speichert dann den aktuellen Timerwert ab.\vspace{11pt}

Der Softwarebaustein zur Drehzahlerfassung ist in zwei Dateien unterteilt, die Dateien \glqq{}rpmMeas.c\grqq{} und \glqq{}rpmMeas.h\grqq{}. Die Datei \glqq{}rpmMeas.h\grqq{} enthält alle relevanten Bibliotheken und Prototypen für die Datei \glqq{}rpmMeas.c\grqq{} (siehe Abbildung \ref{fig:rpmMeasH}). Hier werden auch die beiden Kanäle zur Erfassung der Daten auf das Timer Caputure Register 0 (rechter Antrieb, \glqq{}kCTIMER\_Capture\_0\grqq{}) und auf das Timer Capture Register 1 (linker Antrieb, \glqq{}kCTIMER\_Capture\_1\grqq{}) festgelegt. Bei dem verwendeten Mikrocontroller entspricht dies den Pins P0.25 (rechts) und P0.24 (links). Der Pin P0.25 wird auf der Controllerplatine über den Pin4 und der Pin P0.24 über den Pin6 der Buchsenleiste J13 nach außen geführt.\vspace{11pt}

\begin{figure}[H] %H für Positionierung hier
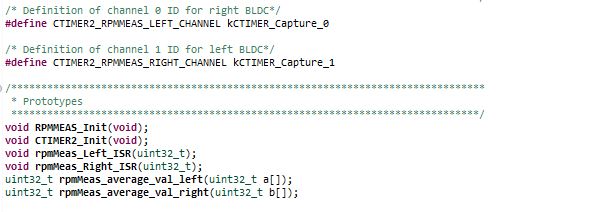
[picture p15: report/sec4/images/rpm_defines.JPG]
 
\centering
\captionsetup{width=.95\textwidth}
\caption[Relevante Zeilen der Datei \glqq{}rpmMeas.h\grqq{}]{Relevante Zeilen der Datei \glqq{}rpmMeas.h\grqq{} zur Initialisierung des Timers CTIMER2 für die Zeiterfassung zwischen zwei Flanken Signal sowie die Prototypen für die Funktionen aus der Datei \glqq{}rpmMeas.c\grqq{}}\centering
\label{fig:rpmMeasH}
\end{figure}

Die Datei \glqq{}rpmMeas.c\grqq{} enthält die Funktionen zur Initialisierung der für die Verwendung der Drehzahlerfassung notwendigen Controller-Peripherie als auch die Definition und Initialisierungen der notwendigen Parameter zur Erfassung und Berechnung der benötigten Drehzahlwerte (siehe Abbildung \ref{fig:rpmMeasC0}).\vspace{11pt}

In der Funktion RPMMEAS\_Init wird zuerst die Funktion CTIMER2\_Init aufgerufen, welche unter anderem die beiden vorher festgelegten Kanäle des Timers CTIMER2 (\glqq{}kCTIMER\_Capture\_0\grqq{} und \glqq{}kCTIMER\_Capture\_1\grqq{}) initialisiert. Bei der Initialisierung der Capture Channel (CTIMER\_SetupCapture) wird das entsprechende Ereignis, bei dem ein Capture stattfinden soll, festgelegt. In diesem Fall wird dises Ereignis für beide Kanäle auf die steigende Flanke gesetzt und die Capture Interrupt Requests aktiviert (\glqq{}kCTIMER\_Capture\_RiseEdge\grqq{}).

\begin{figure}[H] %H für Positionierung hier
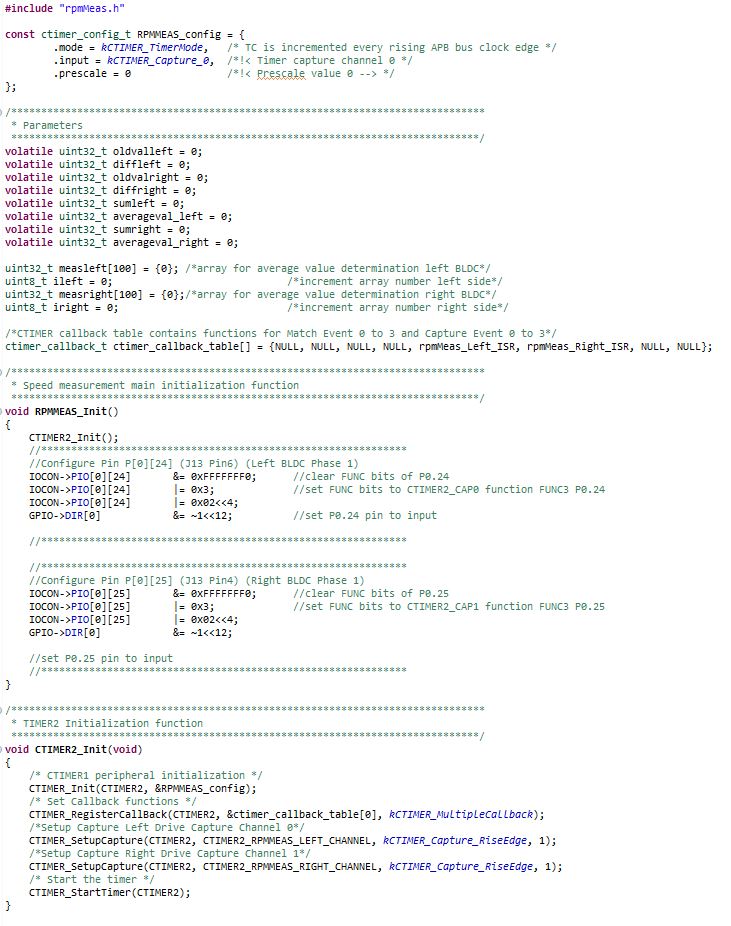
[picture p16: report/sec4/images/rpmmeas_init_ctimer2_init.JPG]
 
\centering
\captionsetup{width=.95\textwidth}
\caption[Funktionen RPMMEAS\_Init und CTIMER2\_Init in der Datei \glqq{}rpmMeas.c\grqq{}]{Funktionen RPMMEAS\_Init und CTIMER2\_Init in der Datei \glqq{}rpmMeas.c\grqq{}}\centering
\label{fig:rpmMeasC0}
\end{figure}

Damit beim Auftreten einer steigenden Flanke der Rechtecksignale ein Interrupt Request ausgelöst werden kann, benötigt man zunächst den Parameter cTimer\_callback\_table. Die Callback-Table enthält die bei verschiedenen Events (Match0-3 und Capture0-3) aufzurufenden Interrupt Service Routinen rpmMeas\_Left\_ISR (Capture Event 0) und rpmMeas\_Right\_ISR (Capture Event 1). Die Callback-Table wird als Pointer-Array der Funktion CTIMER\_RegisterCallBack übergeben. Bei einer Callback-Funktion, auch Rückruffunktion genannt, wird einer Funktion als Parameter eine weitere Funktion oder wie hier eine Liste von Funktionen übergeben. Des weiteren muss in der RegisterCallBack-Funktion der Typ des Callbacks festgelegt werden. In diesem Fall wird der Callback als \glqq{}kCTIMER\_MultipleCallback\grqq{} festgelegt, was bedeutet, dass pro Kanal ein Callback durchgeführt werden kann. Zuletzt wird in der CTIMER2\_Init der Timer CTIMER2 gestartet.\vspace{11pt}

Nach Vollendung der Initialisierungen in der Funktion CTIMER2\_Init werden in der Funktion RPMMEAS\_Init zusätzlich die Pins P0.24 (Messung links) und P0.25 (Messung rechts) für die Verwendung als Capture Input Pin des Timers CTIMER2 konfiguriert.\vspace{11pt}

Zur Erfassung der Drehzahl wird im Programm eine Interrupt Service Routine rpmMeas\_Left\_ISR und rpmMeas\_Right\_ISR für die jeweilige Antriebsseite benötigt. Sobald auf eine steigende Flanke getriggert wird, wird durch das Setzen eines Interrupt Flags die Interrupt Service Routine ausgelöst. In der jeweiligen Service Routine wird der aktuelle Zähler-Wert des Timers CTIMER2 mit dem Befehl CTIMER\_GetTimerCountValue ausgelesen, der Wert bei der letzten Flanke abgezogen und somit die verstrichene Zeit zwischen diesen Flanken berechnet (diffright und diffleft) und den Arrays zur Mittelwertberechnung (measright[ ], measleft[ ]) übergeben.  

\begin{figure}[H] %H für Positionierung hier
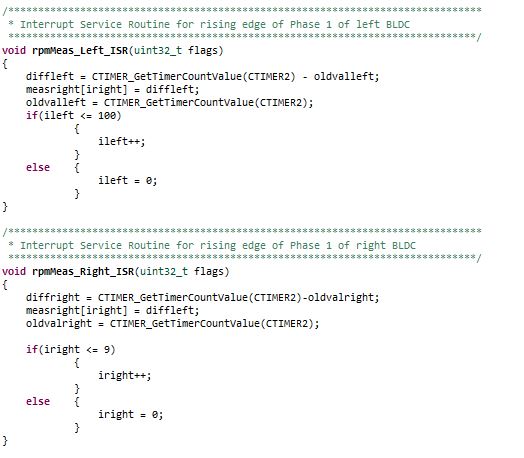
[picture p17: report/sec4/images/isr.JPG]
 
\centering
\captionsetup{width=.95\textwidth}
\caption[Interrupt Service Routinen für Zeitermittlung zwischen zwei Capture-Flanken]{Interrupt Service Routinen für Zeitermittlung zwischen zwei Flanken der Capture Inputs des Timers CTIMER2}\centering
\label{fig:isr}
\end{figure}

\newpage
Von den in den Arrays (\glqq{}measright[ ]\grqq{} und \glqq{}measleft[ ]\grqq{}) gespeicherten Werten können in den Funktionen \glqq{}rpmMeas\_average\_val\_right()\grqq{} und \glqq{}rpmMeas\_average\_val\_right()\grqq{} die Mittelwerte gebildet werden. Die Mittelwerte \glqq{}average\_val\_right\grqq{} und \glqq{}average\_val\_left\grqq{} werden in den weiteren Schritten zur Implementierung der Drehzahlregelung benötigt. 

\begin{figure}[H] %H für Positionierung hier
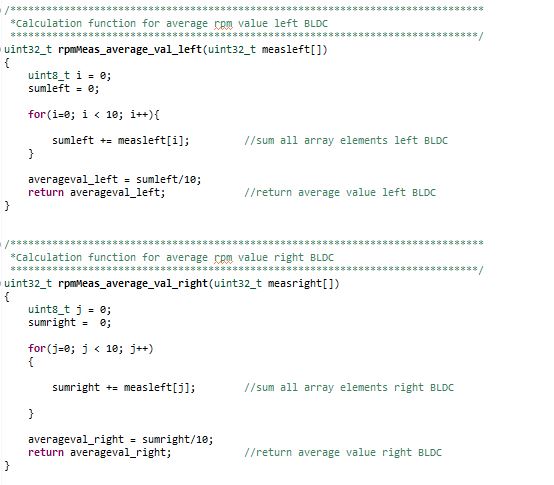
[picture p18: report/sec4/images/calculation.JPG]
 
\centering
\captionsetup{width=.95\textwidth}
\caption[Funktionen zur Berechnung des Mittelwerts der Zeiten zwischen den Capture-Flanken]{Funktionen zur Berechnung des Mittelwerts der erfassten Zeiten zwischen den Flanken der Capture Inputs des Timers CTIMER2}\centering
\label{fig:calculation}
\end{figure}

\newpage
\subsubsection{Ausblick Schaltungserweiterung}\label{Sec4Sub5Sub4}
 
Nachdem die Referenzspannung Vref in der Schaltung so dimensioniert ist, dass in der Theorie alle Drehzahlen zuverlässig als eindeutiges Rechtecksignal dargestellt werden können, treten in der Praxis dennoch Probleme auf. Drehzahlen im sehr niedrigen Drehzahlbereich (ca. 1,09 ms bis 1,10ms PWM-Pulsbreite) oder auch im höheren Drehzahlbereich (über 1,5ms) werden nicht immer zuverlässig zu einem eindeutiges Rechtecksignal verarbeitet, da die Referenzspannung keine eindeutigen Schnittpunkte mit dem Eingangssignal besitzt (siehe Abbildung \ref{fig:ProblematikStopThrottle}). Auch ein Abfallen der Batteriespannung bei längerem Betrieb des Fahrzeugs kann ebenfalls das Problem verursachen, dass verschiedene Drehzahlen (vor allem an den Maxima) nicht mehr detektiert werden können.
 
\begin{figure}[H] %H für Positionierung hier
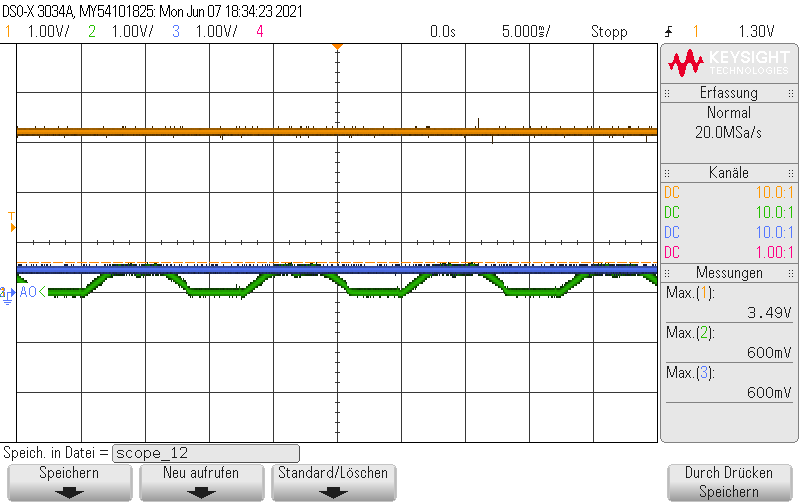
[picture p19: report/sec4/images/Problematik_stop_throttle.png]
 
\centering
\captionsetup{width=.95\textwidth}
\caption[Fehlerhafte Rechtecksignal-Erzeugung bei niedrigen Drehzahlen]{Fehlerhafte Rechtecksignal-Erzeugung (in diesem Fall kein Rechteck) bei niedrigen Drehzahlen, wenn die Schaltschwellen nicht erreicht werden}\centering
\label{fig:ProblematikStopThrottle}
\end{figure}

Eine mögliche Lösung der Problematik ist die Erweiterung des Spannungsteilers für die Referenzspannung des OPV um eine zusätzliche und zuschaltbare Teilerstufe (1x für hohe Drehzahlen; 1x für niedrige Drehzahlen) mit einem n-Kanal MOSFET gegen Masse (siehe Abbildung \ref{fig:Schaltungserweiterung}). Diese Maßnahme ermöglicht es, die Referenzspannung, für hohe und niedrige Drehzahlen flexibel anzupassen um in jedem Fall ein zuverlässiges Ausgangssignal für die Messung der Drehzahl zu erhalten.\vspace{11pt}

Durch die Vorgabe eines bestimmten Modus (MCU-Mode), kann durch die Definition von zwei Drehzahlbereichen (z.B. Pulsbreite 1,09ms - 1,43ms langsam; Pulsbreite 1,43ms - 1,9ms schnell) eine individuelle Referenzspannung von ca. 500mV für langsame Drehzahlen und min. 1V für hohe Drehzahlen eingestellt werden. Der Vorteil ist, dass man dadurch einen bestimmten Toleranzbereich für Schwankungen der Versorgungsspannung erzeugt und die Schaltung dadurch weniger anfällig für Abweichungen ist.\vspace{11pt}

\begin{figure}[H] %H für Positionierung hier
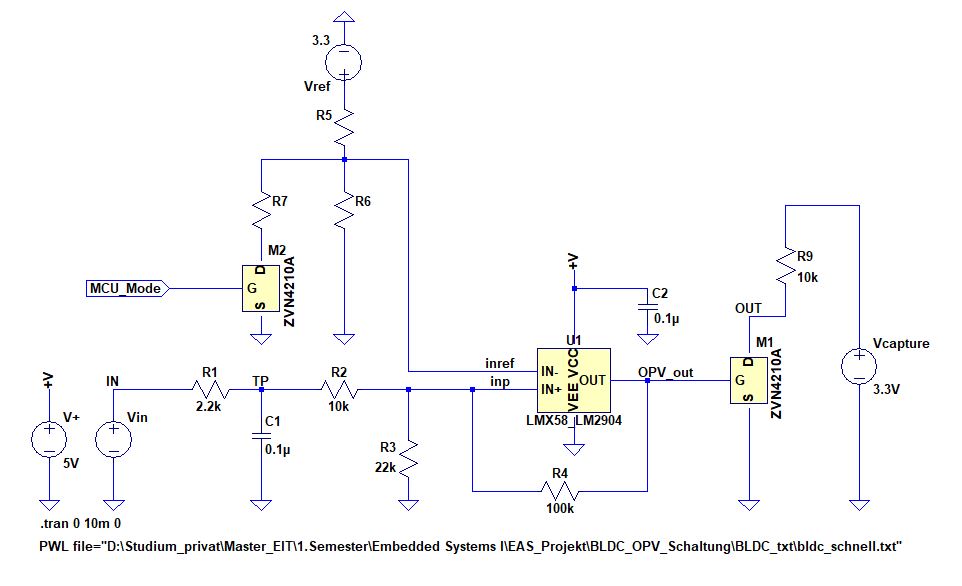
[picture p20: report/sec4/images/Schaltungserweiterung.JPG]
 
\centering
\captionsetup{width=.95\textwidth}
\caption[Schaltplan der Tiefpass-/Komparatorschaltung nach der Schaltungserweiterung]{Schaltplan der Tiefpass-/Komparatorschaltung nach der Schaltungserweiterung um eine zweite Referenzspannungsstufe; erstellt für die Simulation eines Phasensignals in LTspice XVII}\centering
\label{fig:Schaltungserweiterung}
\end{figure}

In der Software muss hierzu in der Interrupt Service Routine der Drehzahlwert-Erfassung eine Umschalterkennung programmiert werden. Diese stellt über einen Ausgang des Mikrocontrollers die Referenzspannungsstufen über einen n-Kanal MOSFET so ein, wie sie bei der aktuellen Drehzahl gerade benötigt werden. Zur Bestimmung der Widerstandswerte für R5, R6 und R7 können die Gleichungen \ref{eq4.3} und \ref{eq4.4} verwendet werden.\vspace{11pt}

\begin{equation}\label{eq4.3}
V_{ModeLow} = \frac{ R6 }{R6 + R5 }\cdot 3,3V
\end{equation}

\begin{equation}\label{eq4.4}
V_{ModeHigh} = \frac{ R7 || R6 }{(R7 || R6) + R5}\cdot 3,3V
\end{equation}

\newpage

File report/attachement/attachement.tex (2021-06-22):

%***********************************************************************
%***************************** Attachement *****************************
%***********************************************************************

%********************************************
%************** Schaltplan ***************

\pagestyle{fancy}
\rhead{\thepage} \chead{} \lhead{\nameref{SecAtt1}}
\cfoot{}

\addcontentsline{toc}{section}{Anhang}

\section*{Anhang 1: Schaltplan} \label{SecAtt1}
\begin{figure}[H] %H für Positionierung hier
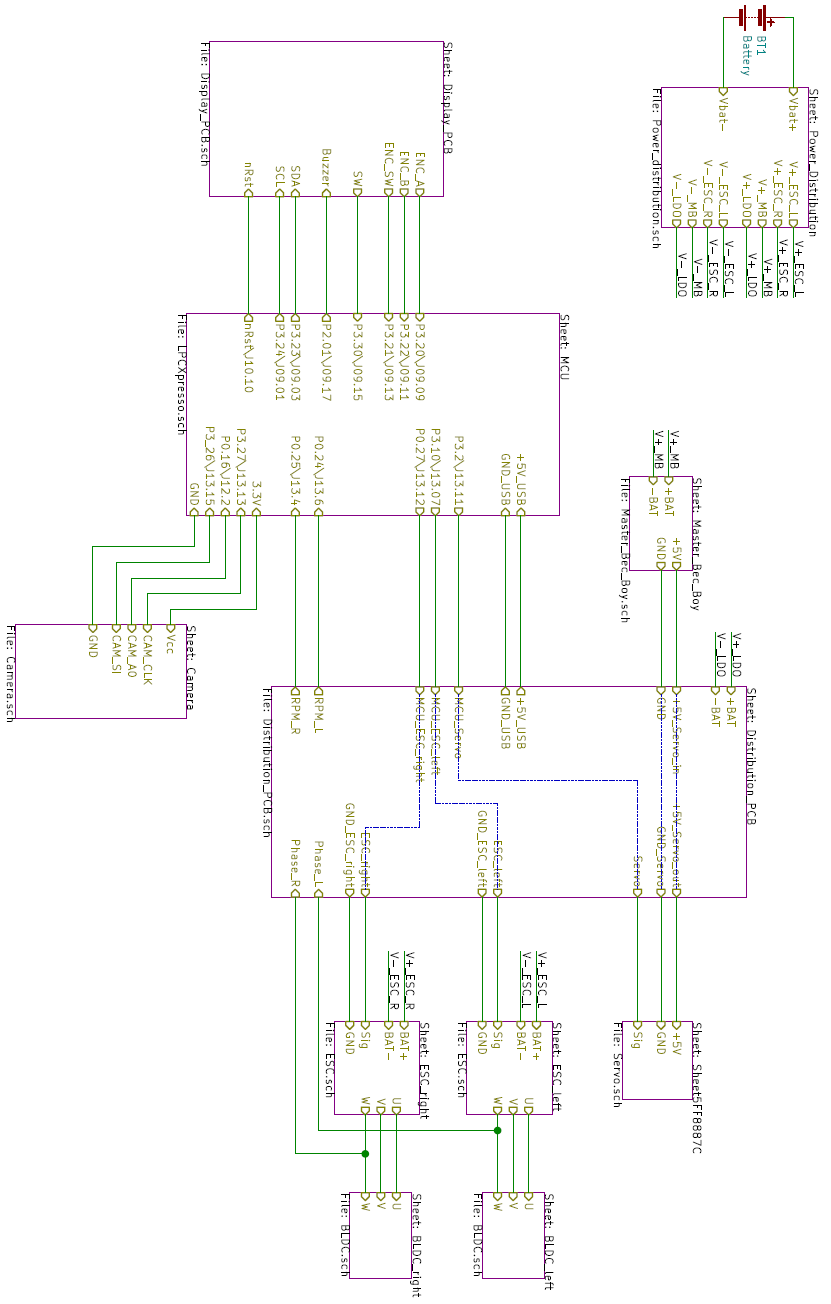
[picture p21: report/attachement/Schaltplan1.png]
 
\centering
\label{Att:Schaltplan1}
\end{figure}
\begin{figure}[H] %H für Positionierung hier
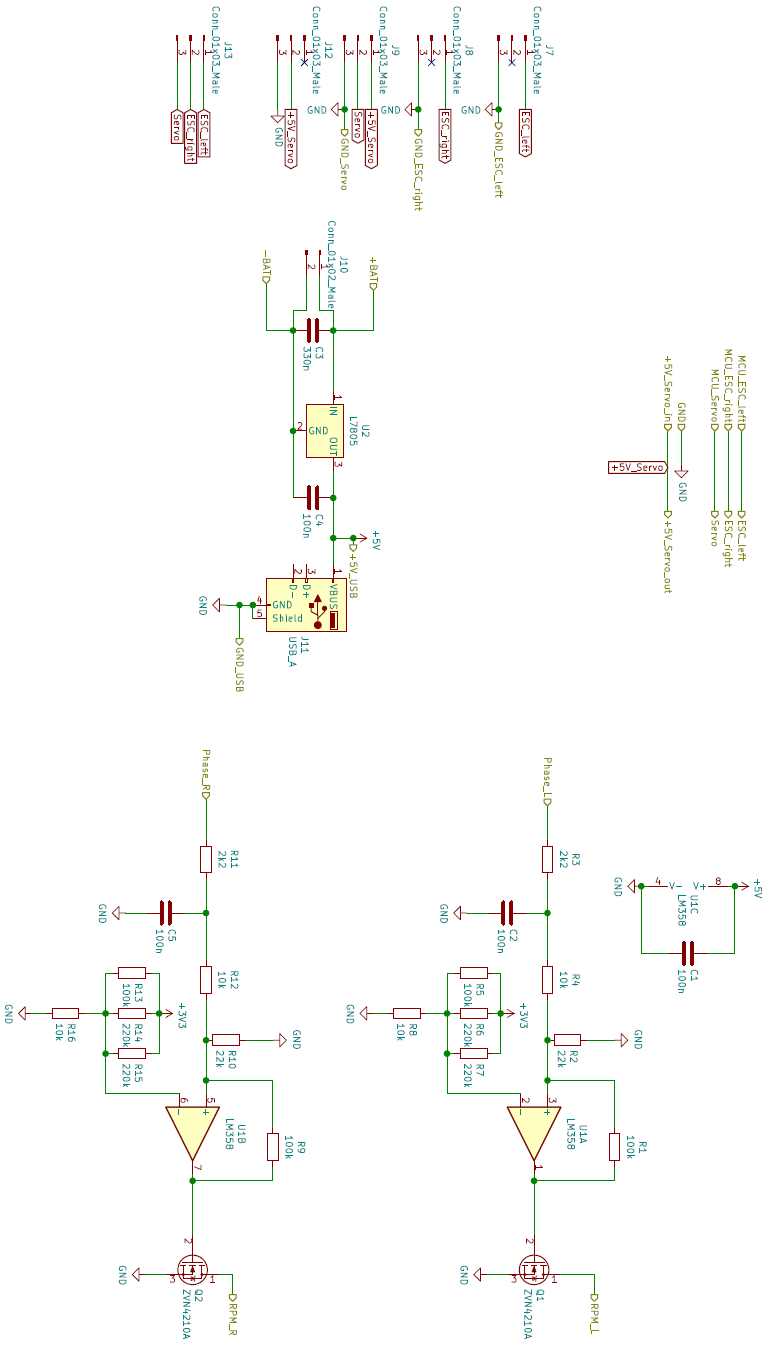
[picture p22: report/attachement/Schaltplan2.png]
 
\centering
\label{Att:Schaltplan2}
\end{figure}

\newpage
\pagestyle{fancy}
\rhead{\thepage} \chead{} \lhead{\nameref{SecAtt2}}
\cfoot{}

\section*{Anhang 2: Pin Assignment} \label{SecAtt2}
\begin{figure}[H] %H für Positionierung hier
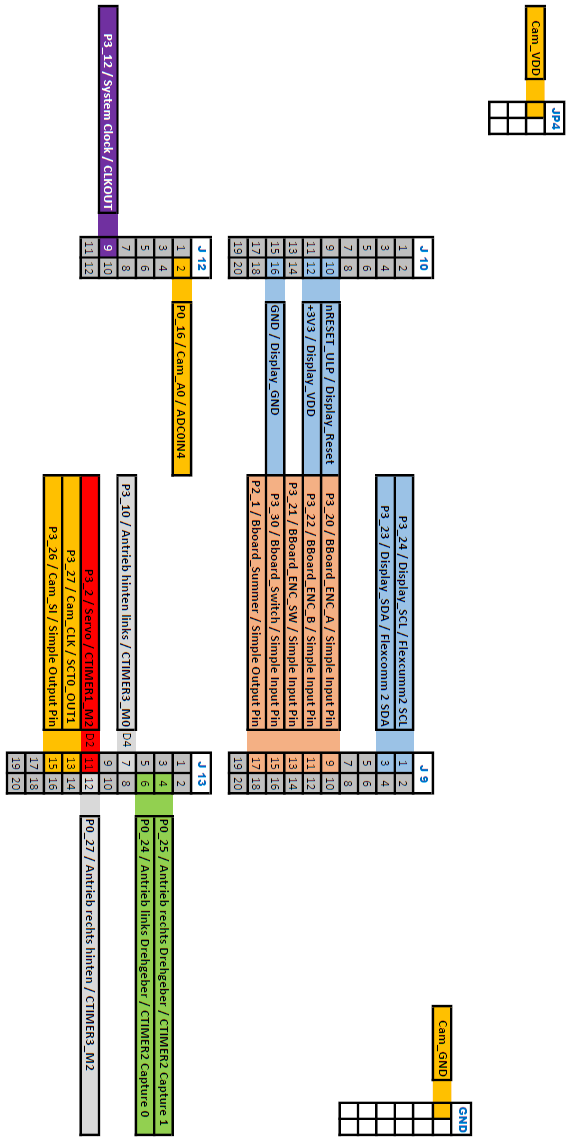
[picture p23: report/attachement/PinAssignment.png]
 
\centering
\label{Att:PinAssignment}
\end{figure}

\newpage

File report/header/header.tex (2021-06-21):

%***********************************************************************
%*************************** Document Header ***************************
%***********************************************************************

% Document formatting
\documentclass[a4paper,11pt]{article} %document type
\usepackage[a4paper, left=3cm, right=2.5cm, bottom=3cm]{geometry}  %borders
\usepackage{fancyhdr} %pagestyle
\setlength{\headheight}{15pt} %page header height
\usepackage[normalem]{ulem} %underline not only with line (eg. dotty )
\usepackage{amsfonts}	%Für Schriftarten
\usepackage[onehalfspacing]{setspace} %linespace
\usepackage{indentfirst} %ersten Paragraph des Kapitels einrücken

% Character set and orthography
\usepackage[utf8]{inputenc} %UTF8, also mit Umlauten
\usepackage[ngerman]{babel}	%Deutsche Rechtschreibung
\usepackage[T1]{fontenc}	%Westeuropäische Codierung

% Graphics
\usepackage{graphicx}
\usepackage{float} %[H] for placement forcing
\usepackage{caption} %captionsetup

% Acronyms
\usepackage[printonlyused]{acronym}

% References
\usepackage{titleref} %for \ref
\usepackage[colorlinks=true,urlcolor=blue,linkcolor=black,citecolor=black]{hyperref}

% URL
\usepackage{url} 
\newcommand*\oldurlbreaks{}
\let\oldurlbreaks=\UrlBreaks
\renewcommand{\UrlBreaks}{\oldurlbreaks\do\a\do\b\do\c\do\d\do\e%
  \do\f\do\g\do\h\do\i\do\j\do\k\do\l\do\m\do\n\do\o\do\p\do\q%
  \do\r\do\s\do\t\do\u\do\v\do\w\do\x\do\y\do\z\do\?\do\&\do\-}

%\usepackage{ragged2e}	%justification (block)
%\PassOptionsToPackage{hyphens}{url}
%\usepackage{scrextend} %Koma Blocksatz
%\usepackage{tabularx} %Tabellen verwenden

%\usepackage[numbers]{natbib} %Für deutsches Literaturverzeichnis

%\usepackage{blindtext}
\usepackage{siunitx}
\sisetup{locale = DE}
\usepackage{tikz}
\usetikzlibrary{shapes.geometric, arrows}
\usetikzlibrary{calc} 
\tikzstyle{startstop} = [rectangle, rounded corners, minimum width=3cm, minimum height=0.5cm,text centered, draw=black, fill=red!30]

\tikzstyle{process} = [rectangle, minimum width=3cm, minimum height=0.5, text centered, text width=3cm, draw=black, fill=orange!30]

\tikzstyle{io} = [trapezium, trapezium left angle=70, trapezium right angle=110, minimum width=3cm, minimum height=0.5, text centered, text width=2cm, draw=black, fill=blue!30]

\tikzstyle{decision} = [diamond, minimum width=3cm, minimum height=0.5, text centered, draw=black, fill=green!30]

\tikzstyle{arrow} = [thick,->,>=stealth]

\usepackage[european]{circuitikz}
%\usepackage{enumitem,amssymb}
%\newlist{checklist}{itemize}{2}
%\setlist[checklist]{label=$\square$}

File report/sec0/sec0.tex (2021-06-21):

%*****************************************************************
%*************************** Section 0 ***************************
%**************************** Vorwort ****************************
%*****************************************************************

\pagestyle{fancy}
\rhead{\thepage} \chead{} \lhead{\nameref{Sec0}}
\cfoot{}

\addcontentsline{toc}{section}{Vorwort und Projekt-Links}
\section*{Vorwort und Projekt-Links}\label{Sec0}

Dieser Bericht umfasst die bei der Durchführung des Projekts \glqq{}Aufbau und Programmierung eines Modellfahrzeugs für den  \ac{NXP}-Cup\grqq{} über den Zeitraum von zwei Semestern gesammelten Erfahrungen und Ergebnisse. Wir als Projektteam bedanken uns herzlich bei Herrn Prof. Dr. Rausch und Herrn Arne Kullina für die Unterstützung bei diesem Projekt.\vspace{11pt} 

Wir freuen uns außerdem darüber, dass wir bei der Innovation Challenge von electromaker.io den dritten Platz mit unserem Projekt belegen konnten. Da Electromaker ein Partner von NXP ist, muss jedes Team ihr Projekt auf der Plattform electromaker.io veröffentlichen, um am \ac{NXP}-Cup teilnehmen zu können. Besonders gut dokumentierte oder interessante Fahrzeug-Projekte können bei der Innovation Challenge im Vorfeld des \ac{NXP}-Cups ein Preisgeld von bis zu 1000€ gewinnen.\vspace{11pt}

\begin{center}
\textbf{Unsere Projektdokumentation auf electromaker.io}\\
\textbf{findet sich unter diesem Link:}\vspace{9pt} 

\url{https://www.electromaker.io/project/view/fast-and-furious}

\end{center}

Sowohl die gesamte Dokumentation (Stromlaufpläne, Bilder, Pinbelegungen, 3D-Druck-Dateien, Datenblätter, ...), als auch den Programmcode, haben wir auf GitHub veröffentlicht. Wir hoffen, dass das nächste Team der HAW Landshut (Hochschule für angewandte Wissenschaften Landshut) auf unsere ausführlich dokumentierte Grundlage aufbauen und den NXP-Cup gewinnen wird.\vspace{11pt} 

\begin{center}
\textbf{Der Programmcode und die Projektdokumentation}\\
\textbf{finden sich unter diesen Links:}\vspace{9pt} 

\url{https://github.com/CEcker94/nxp-aes-proj}\vspace{5pt} 

\url{https://github.com/CEcker94/nxp-aes-documentation}

\end{center}

\newpage

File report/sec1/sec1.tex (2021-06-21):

%*****************************************************************
%*************************** Section 1 ***************************
%************************** Einfuehrung **************************
%*****************************************************************

%\pagestyle{fancy}
\rhead{\thepage} \chead{} \lhead{\ref{Sec1}. \nameref{Sec1}}
\cfoot{}

\section{Einführung}\label{Sec1}

\subsection{Zielsetzung}\label{Sub1Sec1}

Das Ziel der Projektarbeit ist der Aufbau und die Programmierung eines Modellfahrzeugs für den \ac{NXP}-Cup mit einem eigens gebauten, selbstfahrenden Fahrzeug. Bei diesem Wettbewerb müssen die im Maßstab 1:18 angefertigten Fahrzeuge einen Parcours in möglichst kurzer Zeit selbstständig durchfahren. Diese werden von Studenten aus Europa, dem mittleren Osten und Afrika auf Grundbasis eines Bausatzes entwickelt. Die Fahrbahn wird von zwei schwarzen Streifen begrenzt, die auf einem weißen Hintergrund aufgebracht sind. Das Fahrzeug muss diese Begrenzungen erkennen und anhand deren Auswertung die Geschwindigkeit und den Lenkwinkel anpassen. Angetrieben wird das Auto mithilfe zweier \acp{BLDCMot}. Die Lenkung wird mittels Servoantrieb und Lenkgestänge realisiert. Auf dem Fahrzeug dürfen beliebig viele Prozessoren und Bauteile von NXP Semiconductors, welche den Wettbewerb ausrichten, verwendet werden~\cite{MWil}. Sind für das eigene Fahrzeug benötigte Komponenten nicht im Portfolio von NXP Semiconductors vorzufinden, können auch eigene oder die Produkte anderer Hersteller verwendet werden. 

\subsection{Konzept}\label{Sub1Sec2}

Zu Beginn soll das Fahrzeug mit dem Standardbausatz zusammengebaut werden. Die Software wird aus bereits vorhandenen, vorherigen Projekten zusammengesetzt und optimiert. Ein großes Augenmerk liegt dabei auf einem übersichtlicheren Aufbau des Programms und besserer Nachvollziehbarkeit durch Kommentation und eingängigerer Benennung der Funktionen und Parameter.\vspace{11pt}

Die Programmierung soll Stück für Stück vorgenommen werden. Zu Beginn wird die Ansteuerung der \acp{BLDCMot} bearbeitet. Ist der Punkt erreicht, an dem die Motoren angesteuert und die Drehzahl über die Puls-Weiten-Modulation variiert werden kann, soll eine Möglichkeit der Drehzahlerkennung erarbeitet werden. Im Anschluss an die Inbetriebnahme der Antriebe wird die Software für den Servomotor der Lenkung erstellt. Die Bedienung des Fahrzeugs soll über ein \ac{OLED}, einen Drehencoder und einen Taster realisiert werden. Zur Streckenerkennung wird eine Zeilenkamera verwendet. Bei Bedarf kann zusätzlich oder ersatzweise eine größere Kamera eingesetzt werden. Nach der Inbetriebnahme der Einzelkomponenten werden deren Ansteuerung und Auswertung mithilfe einer Regelung verknüpft. Die Software des Fahrzeugs soll am Ende so optimiert werden, dass es schnellstmöglich, aber auch sicher durch den Parcours fährt.\vspace{11pt}

Nach der erfolgreichen Entwicklung des Fahrzeugs für das Durchfahren des Parcours soll für eine zusätzliche Wettbewerbsdisziplin eine Objektdetektion mithilfe eines Ultraschallboards realisiert werden, welches bereits in den vorherigen Semestern von anderen Studierenden entwickelt wurde. Mithilfe dieses Ultraschall-Boards soll das Fahrzeug Hindernisse erkennen und um diese herumfahren können.\vspace{11pt}

Karosserieteile, wie beispielsweise eine  Akkuhalterung oder eine Stoßstange mit der Möglichkeit zur Befestigung des Ultraschallboards, werden mit einem 3D-Druck-Verfahren erstellt. Dafür werden vor allem Teile gedruckt, welche bereits von Herrn Arne Kullina im Rahmen seines Praktikums bei Herrn Prof. Dr. Mathias Rausch im Sommersemester 2020 konstruiert wurden.\vspace{11pt}

Für eine übersichtlichere Kabelführung und einfachere De- und Montage werden zwei Verteilerplatinen (Lochrasterplatinen) mit Steck- und Schraubkontakten erstellt, an welchen die Einzelkomponenten angeschlossen werden.

\newpage

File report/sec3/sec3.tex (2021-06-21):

%*****************************************************************
%*************************** Section 3 ***************************
%************* Controllerplatine und Programmiertool *************
%*****************************************************************

\pagestyle{fancy}
\rhead{\thepage} \chead{} \lhead{\ref{Sec3}. \nameref{Sec3}}
\cfoot{}

\section{Controllerplatine und Programmiertool}\label{Sec3}

Für dieses Projekt wird die Controllerplatine LPCXpresso54628 von NXP Semiconductors verwendet. Das Herzstück dieser Platine ist der auf dem ARM Cortex-M4 basierende Mikrocontroller LPC54628. Dieser Controller wird wegen seiner schnellen Taktfrequenz und seiner großen Anzahl an Peripherie für die Ansteuerung der Motoren und des Servos sowie für die Sensorik zur Bestimmung des Streckenverlaufs verwendet. Der Vorteil einer fertigen Controllerplatine liegt darin, dass der Schaltplan sowie das dazugehörige Layout professionell erstellt sind, wodurch dieser aufwendige Schritt bei der Entwicklung des Autos entfällt und die einwandfreie Funktionsweise des Controllers sichergestellt wird. Außerdem ist darauf bereits ein Debugger zur Programmierung und Fehlersuche verbaut. Durch das Flashen dieses Debuggers über das Programm \glqq{}LPCScrypt\_2.1.2\_57\grqq{} kann zwischen dem J-Link Debugger (Standardinstallationspfad + scripts/program\_JLINK.cmd) und dem NXP-eigenen LinkServer Debugger (Standardinstallationspfad + scripts/program\_CMSIS.cmd) gewählt werden. 

\begin{figure}[H] %H für Positionierung hier
	 
	\centering
	\captionsetup{width=.95\textwidth}
	\caption[Controllerplatine LPCXpresso54628 ~\protect\cite{Semic}]{Draufsicht auf die Controllerplatine mit dem Mikrocontroller LPC54628  (in rot hervorgehoben) als Hauptbestandteil ~\protect\cite{Semic}}\centering
	\label{fig:Controllerplatine}
\end{figure}

Zur Programmierung des Controllers dient das auf Eclipse basierende Tool \glqq{}MCUXpresso\grqq{}, welches von NXP Semiconductors zur Verfügung gestellt wird. Darin sind die für den verwendeten Controller notwendigen Konfigurationsdateien, wie beispielsweise das Startup-Skript und einige Beispiele, bereits enthalten. Das erleichtert den Einstieg in die Programmierung erheblich. Außerdem kann das Konfigurationstool \glqq{}MCUXpresso Config Tools\grqq{} verwendet werden. Mit diesem kann die Initialisierung der Peripheriebausteine über eine graphische Benutzeroberfläche vorgenommen werden.\vspace{11pt}

Die Pinbelegungen für die in dieser Fahrzeugversion verwendeten Peripherie (Antriebe, Servo usw.) sind im Anhang \glqq{}\nameref{SecAtt2}\grqq{} einsehbar.

\newpage

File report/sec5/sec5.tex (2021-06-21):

%*****************************************************************
%*************************** Section 5 ***************************
%********************* Lenkung des Fahrzeugs *********************
%*****************************************************************

\pagestyle{fancy}
\rhead{\thepage} \chead{} \lhead{\ref{Sec5}. \nameref{Sec5}}
\cfoot{}

\section{Lenkung des Fahrzeugs}\label{Sec5}

Wie in Kapitel \ref{Sec2Sub1} beschrieben, wird das Lenkgestänge des Fahrzeugs von einem Servomotor angetrieben, der im Folgenden näher erklärt wird. Auch auf die Montage der Antriebskomponenten und die Programmierung des Lenkungsbausteins wird in diesem Kapitel näher eingegangen.

\subsection{Servoantrieb}\label{Sec5Sub1}

Zur Lenkung des Fahrzeugs wird ein Servomotor (siehe Abbildung \ref{fig:ServoMotor}) verwendet, der mit den Achsen über ein Lenkgestänge verbunden ist. Ein Servo besteht aus einem Motor, dessen Welle mit einem Potentiometer verbunden ist. Die interne Elektronik regelt automatisch die Istwert-Vorgabe des Potentiometers auf den an der Signalleitung anliegenden Sollwert aus. Dadurch können Lenkwinkelpositionen genau angefahren werden. Die Sollwert-Vorgabe erfolgt, wie die Drehzahlvorgabe bei den \acp{BLDCMot}, mit einem 50Hz \ac{PWM}-Signal und einem Tastgrad von 5\% bis 10\%, wobei dieser proportional zum Lenkwinkel ist. Bei einem Tastgrad von 7,5\% befindet sich die Lenkung in der Mittelstellung. Kleinere Werte bewirken einen Lenkeinschlag nach links und größere Werte einen Einschlag nach rechts. Der \ac{PWM}-Signalleitung und der dazugehörigen Masseleitung schließt sich noch eine Versorgungsleitung an (5V-Versorgung).

\begin{figure}[H] %H für Positionierung hier
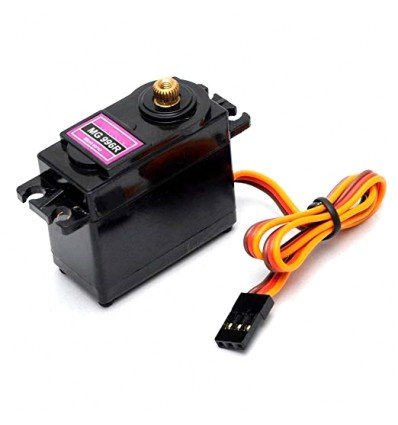
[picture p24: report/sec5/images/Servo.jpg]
 
\centering
\captionsetup{width=.95\textwidth}
\caption[Servomotor mit Anschlussleitungen~\cite{DIYE}]{Servomotor mit Anschlussleitungen; Versorgungsspannung rote Leitung, \ac{PWM}-Signal orangene Leitung und Masseleitung in braun~\cite{DIYE}}\centering
\label{fig:ServoMotor}
\end{figure}

\newpage
\subsection{Montage der Lenkungskomponenten}\label{Sec5Sub2}

Die Komponenten der Lenkung, welche über einen Servomotor und ein mit den Reifen verbundenes Lenkgestänge realisiert ist, sind wie die Antriebskomponenten auf der unteren Fahrzeugebene montiert. Der Servomotor ist mit vier Schrauben an einem losen Teil des Chassis befestigt, welches über zwei Schrauben durch Langlöcher von oben am Fahrzeug montiert ist. Über die Langlöcher kann der Servomotor so platziert werden, dass die Vorderreifen parallel zueinander stehen. An der Welle des Servomotors ist dann das Lenkgestänge befestigt, welches mit den Reifen verbunden ist.\vspace{11pt}

In Abbildung \ref{fig:MontageLenkungskomponenten} sind die montierten Komponenten der Fahrzeuglenkung abgebildet. Die Befestigung des Servomotors ist in violett hervorgehoben, die Befestigung des losen Chassis-Teils in rot, die Lenkgestänge in blau und die Federung in orange.

\begin{figure}[H] %H für Positionierung hier
 
\centering
\captionsetup{width=.95\textwidth}
\caption[Montage der Lenkungskomponenten]{Montage des Servo-Motors, des Lenkgestänges und der Vorderreifen; Befestigung des Servo-Motors in violett, Befestigungsschrauben des losen Chassis-Teils in rot, Lenkgestänge in blau und Federung in orange}\centering
\label{fig:MontageLenkungskomponenten}
\end{figure}

\newpage
\subsection{Programmierung des Lenkungsbausteins}\label{Sec5Sub3}

Der Lenkungsbaustein der Software ist wie der Antriebsbaustein in zwei Dateien unterteilt, die Dateien \glqq{}servo.c\grqq{} und  \glqq{}servo.h\grqq{}. Die Datei \glqq{}servo.h\grqq{} enthält alle relevanten Bibliotheken und Prototypen für die Datei \glqq{}servo.c\grqq{}. Außer der Einbindung der Bibliotheken und der Prototypen der Funktionen aus der Datei \glqq{}servo.c\grqq{} sind hier auch die Parameter für die Initialisierung des Timers für das \ac{PWM}-Signal hinterlegt (Abbildung \ref{fig:ServoH}). 

\begin{figure}[H] %H für Positionierung hier
 
\centering
\captionsetup{width=.95\textwidth}
\caption[Relevante Zeilen der Datei \glqq{}servo.h\grqq{}]{Relevante Zeilen der Datei \glqq{}servo.h\grqq{} mit den Parametern für die Initialisierung des \ac{PWM}-Timers}\centering
\label{fig:ServoH}
\end{figure}

Wie schon beim Antrieb, wird für die \ac{PWM}-Periodendauer bei der Initialisierung ein Wert von 4.400.000 Takten festgesetzt, woraus mit einer \ac{CPU}-Taktfrequenz von 220MHz (220.000.000 Takte pro Sekunde) eine Periodendauer von 20ms resultiert. Die Pulsbreite wird während des Programmablaufs regelmäßig überschrieben, weshalb für die Initialisierung ein Wert von 0 gewählt werden kann. So bewegt sich der Servomotor bei der Initialisierung nicht und es kommt dabei nicht zum Crash.\vspace{11pt}

Der Wert für den linken maximalen Lenkeinschlag (ca. 200.000) entspricht einer \ac{PWM}-Pulsbreite von 0,91ms und der des maximalen rechten Lenkeinschlags (ca. 459.000) einer Breite von 2,08ms. Auch wenn der Servomotor einen Wert zwischen 1ms und 2ms erwartet, kann mit den eben genannten Einstellungen noch ein wenig mehr Lenkeinschlag gewonnen werden. Mit dem Wert der Mittelstellung (ca. 327.000), welcher durch Probieren angenähert wurde, beläuft sich die Pulsbreite auf 1,486ms. Alle drei Extremwerte (\glqq{}servoMiddleValue\grqq{}, \glqq{}servoLeftValue\grqq{}, \glqq{}servoRightValue\grqq{}) sind Parameter, deren Werte aus dem \ac{EEPROM} kommen und welche in der Einheit µs über das Bedienungsboard eingestellt werden können (siehe Abbildung \ref{fig:ServoC0}).

\begin{figure}[H] %H für Positionierung hier
 
\centering
\captionsetup{width=.95\textwidth}
\caption[Extremwerte der Lenkwinkel als Parameter aus dem \ac{EEPROM}]{Extremwerte der Lenkwinkel als Parameter aus dem \ac{EEPROM}, deren Werte über das Bedienungsboard individuell einstellbar sind; Teil der Datei \glqq{}servo.c\grqq{}}\centering
\label{fig:ServoC0}
\end{figure}

\newpage
Auch der \ac{PWM}-Timer benötigt bei der Initialisierung einige Parameter, deren Werte in der Datei \glqq{}servo.h\grqq{} festgelegt sind (\ac{PWM}-Periodendauer, \ac{PWM}-Pulsdauer, Channel). Der Channel wird auf das Timer Match Register 2 festgelegt (\glqq{}kCTIMER\_Match\_2\grqq{}), was bei dem verwendeten Controller dem Pin P3.2 entspricht. Der Pin P3.2 wird auf der Controllerplatine über den Pin 11 der Buchsenleiste J13 nach außen geführt.

\begin{figure}[H] %H für Positionierung hier
 
\centering
\captionsetup{width=.95\textwidth}
\caption[Funktionen SERVO\_Init, CTIMER1\_Init und SERVO\_Demo der Datei \glqq{}drive.c\grqq{}]{Funktionen SERVO\_Init und CTIMER1\_Init und Demonstrations-Task SERVO\_Demo der Datei \glqq{}drive.c\grqq{}}\centering
\label{fig:ServoC1}
\end{figure}

Die Datei \glqq{}servo.c\grqq{} enthält die Funktionen zur Initialisierung der für die Verwendung des Servos notwendigen Controller-Peripherie. In der Funktion SERVO\_Init wird zuerst die Funktion CTIMER1\_Init aufgerufen, welche den Timer mit den in der Datei \glqq{}servo.h\grqq{} festgelegten Parametern als \ac{PWM}-Timer mit einer Periodendauer von 20ms und einer Pulslänge von 0ms initialisiert. Im Anschluss daran wird festgelegt, dass bei einem Timer-Überlauf die neuen Daten für die Pulslänge aus dem Shadow-Register geladen werden. Zum Ändern des Lenkwinkels muss deshalb lediglich ein neuer Wert in das Shadow-Register geschrieben werden. Hier muss allerdings aufgepasst werden, da das Register nicht die Pulsbreite (On-Time) sondern die Off-Time erwartet. Deshalb muss der Wert, der eingetragen wird, der Periodendauer abzüglich der Pulsdauer entsprechen. Zusätzlich wird in der Funktion SERVO\_Init auch der Pin 3.2 für die Verwendung als \ac{PWM}-Ausgang des Timers CTIMER1 konfiguriert (siehe Abbildung \ref{fig:ServoC1}).\vspace{11pt}

Am Ende wird der Wert für die Mittelstellung des Servos in das Shadow-Register geschrieben und ein Task für die Demonstration der Lenkung gestartet (SERVO\_Demo), welcher nach einmaligem Linkslenken, Rechtslenken und nach der Rückkehr in die Mittelstellung ausgesetzt wird. Der Task \glqq{}SERVO\_Demo\grqq{} ist in Abbildung \ref{fig:ServoC2} einsehbar.

\begin{figure}[H] %H für Positionierung hier
 
\centering
\captionsetup{width=.95\textwidth}
\caption[SERVO\_Demo Task der Datei \glqq{}drive.c\grqq{}]{SERVO\_Demo Task der Datei \glqq{}drive.c\grqq{}}\centering
\label{fig:ServoC2}
\end{figure}

\newpage

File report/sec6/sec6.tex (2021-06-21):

%*****************************************************************
%*************************** Section 6 ***************************
%************************ Bedienungs-Board ***********************
%*****************************************************************

\pagestyle{fancy}
\rhead{\thepage} \chead{} \lhead{\ref{Sec6}. \nameref{Sec6}}
\cfoot{}

\section{Bedienungs-Board}\label{Sec6}

Das Bedienungs-Board ist auf der oberen Fahrzeugebene über dem Controller verbaut. Es enthält ein Display, einen Drehencoder mit Taster, einen separaten Taster und einen Summer. Diese Komponenten dienen zum einen der Eingabe von Parametern und der Bedienung des Fahrzeugs durch den Benutzer und zum anderen zum Ablesen der Fahrzeugdaten, wie beispielsweise der Streckenerkennungsdaten der Kamera.

\subsection{Schaltplan}\label{Sec6Sub1}

Das Bedienungs-Board ist eine selbst bestückte Lochrasterplatine, die die Anschlüsse der einzelnen Komponenten auf zwei Stiftleisten zusammenführt. In den Abbildungen \ref{fig:BedienungsBoard1} und \ref{fig:BedienungsBoard2} ist der Schaltplan des Bedienungs-Boards zusehen. Die Buchsenleisten J3 und J4 sind die Anschlüsse des Displays. An die Buchsenleisten J5 und J6 sind die Pins des Drehencoders geführt. Dieser gibt zwei Signale (ENC\_A, ENC\_B) für die Erkennung der Drehrichtung und ein Signal (ENC\_SW) für den Taster aus. Die Signale des Displays, des Drehencoders, des Tasters und des Summers werden an die Stiftleisten J1 und J2 geführt, über die die Verbindung zur Controllerplatine hergestellt wird. Die Einbindung des Bedienungs-Boards in das Gesamtsystem des Fahrzeugs ist über den Anhang \glqq{}\nameref{SecAtt1}\grqq{} nachvollziehbar.

\begin{figure}[H] %H für Positionierung hier
 
\centering
\captionsetup{width=.95\textwidth}
\caption[Schaltplan des Bedienungs-Boards 1]{Schaltplan des Bedienungs-Boards mit den Stiftleisten J1 und J2 zur Verbindung mit dem Mikrocontroller und den Buchsenleisten J3 und J4 für das Display}\centering
\label{fig:BedienungsBoard1}
\end{figure}

\begin{figure}[H] %H für Positionierung hier
 
\centering
\captionsetup{width=.95\textwidth}
\caption[Schaltplan des Bedienungs-Boards 2]{Schaltplan des Bedienungs-Boards mit dem Drehencoder, dem Taster und dem Summer}\centering
\label{fig:BedienungsBoard2}
\end{figure}

\subsection{Programmierung der Steuerelemente}\label{Sec6Sub3}
Die drei Signale des Drehencoders ENC\_A, ENC\_B und ENC\_SW und das Signal SW des Tasters sind als Pulldown-Anschlüsse ausgeführt. Diese Signale werden im Mikrocontroller über einen internen Pull-Widerstand auf \SI{3,3}{\volt} gezogen. Die beiden Signale ENC\_A und ENC\_B liefern zwei um \SI{90}{\degree} verschobene Rechtecksignale, dessen Frequenz sich mit der Drehgeschwindigkeit ändert. Durch den Phasenversatz um \SI{90}{\degree} kann die Drehrichtung bestimmt werden. Dabei wird bei einer Flanke vom Signal \glqq ENC\_A\grqq{} der Spannungspegel vom Signal \glqq ENC\_B \grqq{} bestimmt. Aus der Information, ob es sich um eine fallende oder steigenden Flanke des Signals ENC\_A handelt und ob der Spannungspegel des Signals ENC\_B \SI{3,3}{\volt} oder \SI{0}{\volt} ist, wird die Drehrichtung bestimmt.\vspace{11pt}

Das Signal Buzzer lässt bei anlegen einer Spannung den internen Quarz des Summers mit seiner charakteristischen Frequenz schwingen. Dadurch können Eingaben des Benutzers akustisch bestätigt werden.

\subsubsection{Taster auswerten}\label{sec:Taster}
Im Flussablaufdiagramm in Abbildung \ref{fig:FlussablaufEncTaster} ist zu erkennen, dass beide Taster mit einer Abtastzeit von \SI{10}{\milli\second} eingelesen werden. Da Taster mechanische Bauteile sind, kommt es bei jedem Betätigen zu ungewollten Pegelwechseln, dem sogenannten Prellen. Dies muss verhindert werden, da dadurch ein einzelner Tastendruck als mehrere interpretiert wird. Soll zum Beispiel ein Zähler per Tastendruck inkrementiert werden, wird bei einem prellenden Taster der Zähler pro Druck nicht um einen sondern um mehrere Schritte erhöht. Die Anzahl, um wie viel der Zähler erhöht wird, hängt davon ab, wie viele Pegelwechsel durch das Prellen erzeugt und mit welcher Frequenz der Taster ausgelesen wird. Um das Prellen zu verhindern, wird auf eine Software-Entprellung zurückgegriffen. Dabei wird ein Tastendruck nur erkannt, wenn sich der Spannungspegel des Tasters für vier Abtastzyklen nicht ändert. Dies entspricht bei einer Abtastzeit von \SI{10}{\milli\second} einer Zeit von \SI{40}{\milli\second}. Bei diesem Verfahren ist es wichtig, dass der Taster mindestens die vierfache Zeit der Abtastzeit betätigt wird. Beim Entprellen wird zuerst abgefragt, ob sich der eingelesene Zustand des Tasters zum vorherigen entprellten Zustand geändert hat. Ist dies der Fall wird ein Zähler dekrementiert. Der Zähler zählt dabei von drei bis null. Erreicht dieser den Wert null oder wird ein Zustand eingelesen, der dem zuvor entprelltem Zustand entspricht, wird der Zähler auf den Wert drei zurückgesetzt. Wechselt der Zähler von null auf drei, wird der Tastendruck als solcher erkannt.\vspace{11pt}

\begin{figure}[H]	
\centering
	\begin{tikzpicture}[node distance=1.5cm]
		\node (start) [startstop] {Start};
		\node (prInit) [process, below of=start] {counter = 0};
		\node (EncIn)[io, below of=prInit]{Encoder einlesen};
		\node (prENC) [process, below of=EncIn] {Encoder auswerten};
		\node (decCounter)[decision,below of=prENC,yshift=-0.5cm]{counter$\geq$10?};
		\node (SWIn)[io,below of = decCounter,yshift=-1cm]{Taster einlesen};
		\node (prSW) [process, below of=SWIn] {Taster auswerten};
		\node (prDelay) [process, below of=prSW] {warte \SI{1}{\milli\second}};

		\draw [arrow] (start) -- (prInit);
		\draw [arrow] (prInit) -- (EncIn);
		\draw [arrow] (EncIn) -- (prENC);
		\draw [arrow] (prENC) -- (decCounter);
		\draw [arrow] (decCounter) -- node[anchor=east]{ja} (SWIn);
		\draw [arrow] (SWIn) -- (prSW);
		\draw [arrow] (prSW) -- (prDelay);
		
		\draw [arrow](decCounter) -- node[anchor = south]{nein} ++(3,0)|-(EncIn);
		\draw [arrow](prDelay) |- ++(3,-1)--+(0,6.5);
				
	\end{tikzpicture}
	
	\caption[Flussablaufdiagramm Taster und Drehencoder einlesen]{Flussablaufdiagramm zum Einlesen des Encoders jede Millisekunde und der Taster alle zehn Millisekunden}
	\label{fig:FlussablaufEncTaster}
\end{figure}

Im C-Code wird der Zähler mit zwei 32 Bit Variablen implementiert. Dabei wird aus jeweils einem Bit der beiden Variablen ein 2bit Zähler gebildet. Dadurch entstehen mit nur zwei Variablen insgesamt 32 Zähler, die von drei bis null zählen können. Dies macht jedoch die Implementierung der Zählfunktion schwieriger, da der Zähler nicht mit einem Postdekrement und if-Abfragen realisiert werden kann. Diese Funktionen müssen durch Bitoperationen ersetzt werden, die die ganze 32 Bit Variable abfragen und ändern können (siehe \cite{Debounce}, Kapitel \glqq Timer-Verfahren (nach Peter Dannegger)\grqq).

\subsubsection{Drehencoder auswerten}\label{sec:Drehencoder}
Im Flussablaufdiagramm in Abbildung \ref{fig:FlussablaufEncTaster} werden die beiden um \SI{90}{\degree} phasenverschobenen Signale des Drehencoders mit einem Zeitabstand von \SI{1}{\milli\second} ausgelesen. Im Anschluss daran müssen daraus die Drehrichtung und die Anzahl der gedrehten Schritte ermittelt werden. Dazu wird in einer Variable der aktuell gemessene und der jeweils letzte Wert der beiden Drehencoderanschlüsse als je ein Bit gespeichert. Dabei liegt in Bit0 der aktuelle Zustand von ENC\_B, in Bit1 der aktuelle Zustand von ENC\_A, in Bit2 der letzte Zustand von ENC\_B und in Bit3 der letzte Zustand von ENC\_A. Die daraus entstehende 4bit-Zahl bildet den Index eines Arrays, welches zeigt, ob der Drehencoder nach links oder nach rechts gedreht worden ist. Steht in der Variable zum Beispiel der Wert 1101\textsubscript{2} (13\textsubscript{10}) bedeutet das, dass die vorherigen Zustände HIGH, der aktuelle Zustand ENC\_A LOW und ENC\_B HIGH sind. Daraus ist abzuleiten, dass eine fallende Flanke des Signals ENC\_A und ein HIGH Pegel am Signal ENC\_B anliegt. In dem Array an der Stelle 13 steht der Wert -1, was eine Drehung im Uhrzeigersinn repräsentiert. Im Falle von 1000\textsubscript{2} (8\textsubscript{10}) liegt eine fallende Flanke an ENC\_A und ein LOW Pegel an ENC\_B an. Daraus ergibt sich im Array der Wert 1 an der Stelle acht, was eine Drehrichtung gegen den Uhrzeigersinn darstellt (siehe \cite{ENC}).
\newpage
\subsection{Programmierung der Anzeige}\label{Sec6Sub2}
Für die Anzeige von Fahrzeugparametern wird ein 64x128 Pixel großes \ac{OLED} verwendet, dessen Ansteuerung über eine \ac{I2C} Schnittstelle erfolgt.  Mit dem Pin6 von Buchsenleiste J3 wird die \ac{I2C} Adresse auf 3C\textsubscript{16} (GND) oder 3E\textsubscript{16} (\SI{3,3}{\volt}) festgelegt. Dem Schaltplan in Abbildung \ref{fig:BedienungsBoard1} ist zu entnehmen, dass die Adresse auf 3C\textsubscript{16} festgelegt ist. Außerdem wird das Reset Signal des Controllers an den Pin4 der Buchsenleiste J3 angelegt.

\subsubsection{Funktionsweise des \acl{OLED}s}\label{sec:FunktionOLED}
Auf der Platine des Displays ist der Displaycontroller SSD1309 von SOLOMON SYSTECH verbaut. Dieser kommuniziert mit dem Mikrocontroller und steuert die Segment- und COM-Anschlüsse des Displays. Das Display besitzt 64 COM-Anschlüsse für die Kathoden der LEDs und 128 Segmentanschlüsse für die Anoden. Jeder COM-Anschluss entspricht einer Zeile des Displays und jeder Segmentanschluss einer Spalte (siehe Schaltplan in Abbildung \ref{fig:OLEDSchaltplan}). Somit kann durch Auswahl einer Reihe mit einem COM-Anschluss und durch ansteuern des Segmentanschlusses jedes Pixel angesprochen werden. Im Displaycontroller ist ein \ac{RAM} mit 64 Zeilen und 128 Spalten verbaut. Jeder Zeile des Speichers ist eine Zeile des Displays (COM-Anschluss) und jeder Spalte des Speichers eine Spalte des Displays (Segmentanschluss) zugeordnet. Somit ist jedem Bit im \ac{RAM} ein Pixel auf dem Display zugewiesen. Acht Zeilen des Speichers werden zu einer Seite zusammengefasst. Dadurch werden acht Zeilen mit einer 8bit großen Variable angesprochen. Bit0 entspricht der ersten Zeile und Bit7 der achten Zeile der Seite. Ein Bild auf dem Display wird aufgebaut indem zuerst das Segment SEG0 mit einem HIGH Pegel ausgewählt wird und die ersten acht im \ac{RAM} gespeicherten Pixelwerte an den Anschlüssen COM0 bis COM7 angelegt werden. Danach wird das Segment SEG1 ausgewählt und die zweiten acht Pixelwerte an die gleichen COM-Anschlüsse angelegt. Dies wird bis zum letzten Segment fortgeführt. Im Anschluss daran wird wieder das Segment SEG0 ausgewählt. Diesmal werden die Pixelwerte jedoch an die Anschlüsse COM8 bis COM15 angelegt. Nachdem das letzte Segment und die letzten acht COM-Anschlüsse angesteuert worden sind, beginnt der Durchlauf von vorne. In den Einstellungen des Displaycontrollers kann eingestellt werden, von welcher Startseite bis zu welcher Stoppseite die COM-Anschlüsse angesteuert werden. Dadurch können Seiten am oberen und unteren Displayrand ausgelassen und somit der Displaybereich vertikal beschränkt werden. Das Start- und Stoppsegment kann ebenfalls bestimmt und somit der rechte und linke Displayrand beschränkt werden. Außerdem kann die horizontale Orientierung festgelegt werden, indem man die Zuordnung des Segments SEG0 auf die Speicherspalte null oder 127 legt. Dadurch werden die ersten Pixelwerte im Speicher nicht in die Spalte des Segments SEG0 sondern in die Spalte von Segment SEG127 geschrieben. Die Einstellung der vertikalen Orientierung erfolgt mit der Richtung, mit der die Zeilen des Speichers auf die COM-Anschlüsse gelegt werden.

\begin{figure}[H]
\begin{circuitikz}
\draw 	(0,0)node[anchor=south]{SEG0}to[short,o-*](0,-1) to[led,-*] (0,-3)
		(2,0)node[anchor=south]{SEG1}to[short,o-*](2,-1) to[led,-*] (2,-3)
		(4,-2)node[circ]{}
		(5,-2)node[circ]{}
		(6,-2)node[circ]{}
		(8,0)node[anchor=south]{SEG127}to[short,o-*](8,-1) to[led] (8,-3)
				
		(1,-3)node[jump crossing](j00){}
		(3,-3)node[jump crossing](j10){}
		
		(-1,-3)node[anchor=east]{COM0}to[short,o-](j00.west) 
		(j00.east)--(j10.west)
		(j10.east)--(3.5,-3)
		(7.5,-3)--(8,-3)

		(0,-4)to[led,-*] (0,-6) (0,-1)-|(j00.north)(j00.south)to[short,-*](1,-4)--(0,-4)
		(2,-4)to[led,-*] (2,-6)	(2,-1)-|(j10.north)(j10.south)to[short,-*](3,-4)--(2,-4)
		(4,-5)node[circ]{}
		(5,-5)node[circ]{}
		(6,-5)node[circ]{}
		(8,-4)to[led] (8,-6)	(8,-1)--(9,-1)to[short,-*](9,-4)--(8,-4)
		
		(1,-6)node[jump crossing](j01){}
		(3,-6)node[jump crossing](j11){}		
			
		(-1,-6)node[anchor=east]{COM1}to[short,o-](j01.west) 
		(j01.east)--(j11.west)
		(j11.east)--(3.5,-6)
		(7.5,-6)--(8,-6)
		
		(1,-4)--(j01.north)	(j01.south)--(1,-6.5)
		(3,-4)--(j11.north)	(j11.south)--(3,-6.5)
		(9,-4)--(9,-6.5)

		(0,-7)node[circ]{}
		(0,-7.5)node[circ]{}
		(0,-8)node[circ]{}
		
		(2,-7)node[circ]{}
		(2,-7.5)node[circ]{}
		(2,-8)node[circ]{}
		
		(8,-7)node[circ]{}
		(8,-7.5)node[circ]{}
		(8,-8)node[circ]{}

		(0,-9)to[led,-*] (0,-11) 	%(0,-1)-|(j00.north)(j00.south)to[short,-*](1,-4)--(0,-4)
		(2,-9)to[led,-*] (2,-11)	%(2,-1)-|(j10.north)(j10.south)to[short,-*](3,-4)--(2,-4)
		(4,-10)node[circ]{}
		(5,-10)node[circ]{}
		(6,-10)node[circ]{}
		(8,-9)to[led] (8,-11)		%(8,-1)--(9,-1)to[short,-*](9,-4)--(8,-4)

		(-1,-11)node[anchor=east]{COM63}to[short,o-](3.5,-11)(7.5,-11)--(8,-11)
		(0,-9)-|(1,-8.5)
		(2,-9)-|(3,-8.5)
		(8,-9)-|(9,-8.5)	
;

\draw[dotted]
	(3.5,-3)--(7.5,-3)
	(3.5,-6)--(7.5,-6)
	(3.5,-11)--(7.5,-11)

	(1,-6.5)--(1,-8.5)
	(3,-6.5)--(3,-8.5)
	(9,-6.5)--(9,-8.5)
;
\end{circuitikz}
\caption[Schaltplan OLED]{Repräsentativer Schaltplan des \acp{OLED} mit Segment- und COM-Anschlüssen}
\label{fig:OLEDSchaltplan}
\end{figure}

\subsubsection{I2C Ansteuerung}\label{sec:OLEDI2C}
%i2c_rtos_interface.c
%ssd1309.c
%ssd1309_rtos.c

Die Kommunikation mit dem \ac{OLED} erfolgt mit einer \ac{I2C} Schnittstelle. Dazu wird auf dem Mikrocontroller ein sogenanntes Flexcomm Modul verwendet. Dieses Modul beinhaltet mehrere Schnittstellen wie zum Beispiel \ac{UART} oder \ac{I2C}. Zu Beginn wird der Port-Pin P3.24 als SCL und der Port-Pin P3.25 als SDA des Flexcomm2 Moduls konfiguriert. Danach wird das Modul mit der Funktion \glqq I2C\_MasterInit\grqq{} von NXP so initialisiert, dass die Taktfrequenz des SDA Signals \SI{400}{\kilo\hertz} beträgt. Dabei ergibt sich Problem, dass das Modul zunächst keine Daten sendet. Nach dem Debuggen und Überprüfen jedes Registers des Moduls wird festgestellt, dass der Takt für das Modul deaktiviert ist. Ärgerlich ist das, da bei der Konfiguration auf Funktionen zurückgegriffen wird, die von NXP entwickelt worden sind und funktionieren sollten. Nachdem der Takt (\SI{12}{\mega\hertz}) für das Flexcomm2 Modul aktiviert ist, werden die Daten wie gewünscht über die Schnittstelle gesendet. Jedoch beträgt die von der Initialisierungsfunktion eingestellte Taktfrequenz statt der angegebenen \SI{400}{\kilo\hertz} nur \SI{333}{\kilo\hertz}. Um den Fehler zu finden, wird in den Registern überprüft, welche Werte für die Erzeugung der Taktfrequenz verwendet werden. Zur Erzeugung wird die Taktfrequenz des Flexcomm2 Moduls mit einem Teiler erniedrigt. Mit zwei Werten werden für die HIGH und LOW Zeiten die Anzahl der Takte (Flexcomm-Takt) angegeben. Nach der Initialisierungsfunktion wird ein Teiler von drei und eine HIGH und LOW Zeit von 5 Takten festgelegt. Die Taktfrequenz berechnet sich über Gleichung \ref{eq:I2CTakt}. Setzt man darin die Werte der Register ein, ergibt sich die gewollte Frequenz von \SI{400}{\kilo\hertz}.

\begin{equation}\label{eq:I2CTakt}
\frac{f_{flexcomm}}{DIV_{CLK}\cdot\left(t_{cyc_{HIGH}}+t_{cyc_{LOW}}\right)}
\end{equation}

Im Datenblatt des Mikrocontrollers sind Werte angegeben, mit denen, bei einer Flexcomm-Taktfrequenz von \SI{12}{\mega\hertz}, eine Taktfrequenz der \ac{I2C}-Schnittstelle von \SI{400}{\kilo\hertz} erzeugt wird. Dabei wird ein Teiler von sechs, eine HIGH Zeit von zwei und eine LOW Zeit von drei Taktzyklen verwendet (vgl. \cite{Semic} Seite 462, Tabelle 496). Mit der Gleichung \ref{eq:I2CTakt} berechnet sich die Taktfrequenz der Schnittstelle zu \SI{400}{\kilo\hertz}. Die drei richtigen Werte werden nach der Initialisierungsfunktion per Hand in den Registern gesetzt.\vspace{11pt}

Um den Prozessor zu entlasten, wird auf die zu sendenden Daten per \ac{DMA} zugegriffen. Dadurch werden diese parallel zum Prozessor in das Senderegister des Flexcomm2 Moduls geladen und der Prozessor hält sich nicht mit hin- und herschieben von Daten auf. Zuallererst wird das \ac{DMA} Modul DMA0 mit der von NXP zur Verfügung gestellten Funktion \glqq DMA\_Init\grqq{} initialisiert. Dem Datenblatt wird in Tabelle 300 entnommen, dass der Kanal 5 mit der \ac{I2C} Funktion des Flexcomm2 Moduls verbunden ist. Deshalb wird mit der ebenfalls bereitgestellten Funktion \glqq DMA\_EnableChannel \grqq{} der Kanal 5 freigegeben. Im Anschluss daran wird mit den beiden Funktionen \glqq DMA\_CreateHandle\grqq{} und \glqq I2C\_MasterTransferCreateHandleDMA\grqq{} die Funktionalität des \ac{DMA}s mit dem Flexcomm2 Modul freigegeben.\vspace{11pt}

Mit der Funktion \glqq I2C\_MasterTransferNonBlocking\grqq{} wird eine Übertragung über \ac{I2C} und \ac{DMA} begonnen. Dieser Funktion wird in einer Variable ein Pointer auf die zu sendende Variable und deren Länge übergeben. Sollen anzuzeigende Daten an das \ac{OLED} übertragen werden wird der Funktion ein Pointer auf einen zuvor definierten Displaypuffer und dessen Länge übergeben. Soll eine Konfiguration gesendet werden, muss der Funktion ein Pointer auf eine 8bit Variable und die Länge eins übergeben werden. Die Übergabe in die Funktion erfolgt mit einer \glqq struct\grqq{} Variable, die neben dem Pointer und der Länge noch die Slaveadressse des Displays, eine Variable für die Richtung der Übertragung (schreiben oder lesen) und eine Variable enthält, die angibt, wie die Start- und Stoppbits gesendet werden. Die Auswahl, ob es sich bei den gesendeten Daten um Konfigurations- oder Anzeigedaten handelt, erfolgt über die sogenannte Subadresse. Diese wird im Anschluss an die Slaveadresse übertragen. Deshalb muss der Funktion ebenfalls die Subadresse und deren Länge übergeben werden.

\subsubsection{Konfiguration des Displays}
Zu Beginn werden einige Resetparameter (siehe Tabelle \ref{tab:InitOLED}) übertragen, die das Display zuerst ausschalten und den Kontrast einstellen. Danach wird ein Kommando gesendet, das den Speicher des \ac{OLED} Controllers so einstellt, dass dessen Inhalt direkt auf dem Display angezeigt wird. Eine andere Möglichkeit ist es, den Inhalt des \ac{RAM}s zu ignorieren. Das Display wird im Standard-Modus (Normal Mode) gestartet. Dies bedeutet, dass eine 1 im Speicher die Pixel-LED einschaltet. Wird der horizontale Modus konfiguriert, wie es in dieser Anwendung der Fall ist, wird das Bild, das auf dem Display angezeigt werden soll, wie im Kapitel \ref{sec:FunktionOLED} beschrieben ist, aufgebaut. Der Befehl 40\textsubscript{16} bestimmt die Zeile des Displays, welche dem Anschluss COM0 zugewiesen wird. Durch Ändern dieses Wertes kann der Inhalt des Displays nach oben bzw. unten geschoben werden. Mit dem nächsten Kommando wird die horizontale Orientierung eingestellt. In diesem Fall wird der Inhalt des Speichers von Segment SEG127 nach SEG0 ausgegeben. Mit dem Befehl \glqq scan from COM N-1 to COM0\grqq{} wird die vertikale Orientierung festgelegt, wobei N dem \glqq MUX ratio\grqq{} (Anzahl der COM-Anschlüsse) entspricht. Die Hardware der COM Pins wird auf ihren Reset Wert eingestellt, was bedeutet, dass die geraden Zeilen mit den ersten 32 COM-Anschlüssen und die ungeraden mit den restlichen 32 COM-Anschlüssen verbunden sind. Danach werden die GPIO Pins als Eingänge konfiguriert. Das nächste Kommando stellt die Frequenz des Displays auf ihren korrekten Wert. Außerdem wird die Anzahl der Takte in Phase 1 und 2 auf jeweils zwei Takte gesetzt. In Phase 1 wird das Pixel ent- und in Phase 2 auf ihren neuen Wert aufgeladen. Diese Werte müssen den Kapazitätswerten der Pixel angepasst werden. Das letzte Kommando stellt die Spannung, bezogen auf die Versorgungsspannung des Displays, ein, wenn die COM-Anschlüsse deaktiviert sind. Alle Konfigurationseinstellungen sind im Datenblatt des Display Controllers zu finden (vgl \cite{SSD1309}).\vspace{11pt}

Nach der Konfiguration des Resets erfolgt die Konfiguration, welche für die Anwendung auf dem Fahrzeug passend ist. Dazu wird die horizontale Orientierung so eingestellt, dass die Spaltenadresse 127 im Speicher dem Segment SEG127 entspricht. Ebenso wird die vertikale Orientierung auf einen Wert festgelegt, sodass das Display von den COM-Anschlüssen COM0 nach COM64 angesteuert wird. Am Ende wird das Display eingeschaltet und ist einsatzbereit.

\begin{table}[H]
\centering
	\begin{tabular}{|c|l||c|l|}
	\hline
	AE&Display off&A8&set MUX ratio to\\
	&&3F&64MUX\\
	\hline
	81&Contrast Controll&C8&scan from COM N-1\\
	7F&&&to COM 0\\
	\hline
	A4&display on, output RAM content&D3&no vertical shift\\
	&&00&\\
	\hline
	A6&Normal display mode&DA&set COM pins\\
	&&12&hardware to reset\\
	\hline
	20&Horizontal mode&DC&GPIO pins are inputs\\
	00&&02&\\
	\hline
	21&set column address&D5&increace F\textsubscript{OSC} frequency\\
	00&start address&F0&\\
	7F&end address&&\\
	\hline
	22&set page address&D9&Phase 1 and 2 period to reset\\
	00&to reset value&22&\\
	07&&&\\
	\hline
	40&set display start&DB&set V\textsubscript{COMH} to $0.78 \cdot V_{cc}$\\
	&line to top line&34&\\
	\hline
	A1&column address 127&&\\
	&is SEG0&&\\
	\hline
	\end{tabular}
	\caption[Initialisierungswert \ac{OLED}]{Werte, die der Reihe nach über \ac{I2C} zum \ac{OLED} gesendet werden}
	\label{tab:InitOLED}
\end{table}

\subsection{Darstellungen auf dem \acl{OLED}}\label{sec:OLEDDarstellen}
Die im Folgenden vorgestellten Funktionen werden zur Darstellung von Formen, Text und Zahlen verwendet. Beim Aufruf einer dieser Funktionen wird eine Variable gesetzt, welche anzeigt, dass dem \ac{OLED} neue Daten gesendet werden müssen. In einem Echtzeittask wird diese Variable alle \SI{30}{\milli\second} geprüft und, wenn notwendig, die neuen Daten gesendet und dargestellt. Die Daten werden in einer globalen Variable, dem Displaypuffer \glqq s\_disp\_0\_buffer\grqq{}, gespeichert.

\subsubsection{Pixelansteuerung}\label{sec:OLEDPixel}
Mit der Funktion \glqq ssd1309\_set\_pixel\grqq{} wird ein Pixel an einer vorgegebenen Position, also das anzusprechende Bit im Displaypuffer, gesetzt oder gelöscht.

\subsubsection{Rechteck zeichnen}\label{sec:OLEDRect}
Zur Darstellung von Rechtecken wird die Funktion \glqq ssd1309\_draw\_rect\grqq{} verwendet. Dieser werden die Koordinaten der linken oberen und rechten unteren Ecke und eine Variable übergeben, die festlegt, ob das Rechteck ausgefüllt ist oder nur die Begrenzungslinie angezeigt werden soll. Außerdem muss angegeben werden, ob die Pixel des Rechtecks gesetzt oder gelöscht werden sollen. In der Funktion werden mit zwei Schleifen alle Pixel innerhalb des Rechtecks durchlaufen und für jedes Pixel bestimmt, ob dieses angezeigt werden soll oder nicht. Jedes Pixel wird mit der Funktion \glqq ssd13099\_set\_pixel\grqq{} aus Kapitel \ref{sec:OLEDPixel} im Displaypuffer gesetzt oder gelöscht.

\subsubsection{Buchstabe darstellen}\label{sec:OLEDBuchstabe}
Der Funktion \glqq ssd1309\_write\_char\grqq{} wird eine char Variable übergeben, welche am Display angezeigt werden soll. In \glqq struct\grqq -Variablen mit dem Namen \glqq ssd1309\_font\_t\grqq{} sind für alle darstellbaren Buchstaben und Zeichen Werte hinterlegt, die diese in unterschiedlichen Größen darstellen. In der Funktion selbst wird zu Beginn überprüft, ob das übergebene Zeichen ein darstellbares Ascii-Zeichen ist. Ist dies der Fall, muss abgefragt werden, ob das Zeichen innerhalb des Displays liegt. Wenn ja, wird mit zwei Schleifen für jedes Pixel innerhalb der Höhe und Breite des Zeichens überprüft, ob dieses angezeigt werden soll oder nicht. Pixel, die angezeigt werden, werden mit der Funktion \glqq ssd1309\_set\_pixel\grqq{} aus Kapitel \ref{sec:OLEDPixel} angesprochen. Die Position des Zeichens wird über einen Cursor eingestellt, der vor dem Funktionsaufruf gesetzt werden muss. Nachdem die einzelnen Pixel des Zeichens im Displaypuffer gesetzt bzw. gelöscht worden sind, wird der Cursor automatisch inkrementiert.

\subsubsection{Text darstellen}\label{sec:OLEDText}
Die Funktion \glqq ssd1309\_write\_str\grqq{} stellt am Display einen Text dar, der über einen Pointer auf ein Zeichenarray übergeben wird. Dazu wird die in Kapitel \ref{sec:OLEDBuchstabe} beschriebene Funktion für jedes im Text enthaltene Zeichen ausgeführt. Die Position des Textes wird, wie bei den Buchstaben, über den Cursor eingestellt, welcher vor dem Funktionsaufruf gesetzt werden muss.

\subsubsection{Bilder darstellen}\label{sec:OLEDBild}
Die Funktion \glqq ssd1309\_draw\_img\grqq{} stellt Bilder dar, die als Hexadezimalwert abgespeichert sind. Die Position der linken oberen Ecke muss der Funktion übergeben werden. Das Bild wird in einer \glqq struct\grqq{}-Variable mit dem Namen \glqq ssd1309\_img\_t\grqq{} übergeben, die die Breite und Höhe des Bildes enthält. Ausgegeben wird das Bild mithilfe zweier Schleifen, die für jedes Pixel des Bildes überprüfen, ob dieses angezeigt werden soll oder nicht. Dargestellt werden die einzelnen Pixel mit der Funktion \glqq ssd1309\_set\_pixel\grqq{} aus Kapitel \ref{sec:OLEDPixel}.

\subsection{Menüführung}\label{sec:OLEDMenu}
Auf die einzelnen Parameter und Funktionen des Fahrzeugs wird mit verschiedenen Menüs zugegriffen. Zuallererst wird das Hauptmenü aufgerufen. Darin sind die einzelnen Funktionen in unterschiedliche Menüpunkte aufgeteilt. Der Mikrocontroller nimmt die Menüführung auf Basis der Werte des Drehencoders und der beiden Taster vor. Ein Zustandsautomat entscheidet je nach Bedienung, ob der Hauptbildschirm oder ein Menü angezeigt werden soll. Bevor der Zustandsautomat ausgeführt wird, werden die beiden Zustände der entprellten Taster sowie die Anzahl der Schritte gespeichert, die der Drehencoder in eine bestimmte Richtung getätigt hat. Der Zustandsautomat bestimmt das aktuelle, anzuzeigende Menü und ändert den Displaypuffer so ab, dass dieses dargestellt wird.\vspace{11pt}

\textbf{Es gibt insgesamt vier verschieden Arten von Menüs:}
\begin{itemize}
\item MENU\_LINK
\item MENU\_CHECK
\item MENU\_PAGE
\item MENU\_VALUE
\end{itemize}

Jedes Menü besitzt eine \glqq struct\grqq{}-Variable, in der immer die drei gleichen Eigenschaften enthalten sind; die Bezeichnung, die auf dem \ac{OLED} angezeigt wird, die Menüart und eine Kennzeichnung, ob das Menü angeklickt werden kann oder nicht. Ist das angeklickte Menü ein MENU\_LINK, so öffnet sich das ebenfalls in der \glqq struct\grqq{}-Variable enthaltene Folge-Menü. Ist es von der Art MENU\_CHECK, wird mit einem Klick auf dieses eine, in der \glqq struct\grqq{}-Variable als Pointer gespeicherte, Variable inkrementiert. Durch eine spätere, binäre UND-Operation mit 1, erhält man eine Variable, die bei einem Klick aktiviert bzw. deaktiviert wird (01\textsubscript{2} \& 1 = 1; 10\textsubscript{2} \& 1 = 0). Mit der Betätigung eines Menüs der Art MENU\_PAGE, wird eine darin verlinkte Funktion ausgeführt. Wird ein Menü der Sorte MENU\_VALUE betätigt, wird der Wert einer in der \glqq struct\grqq{}-Variable als Pointer verknüpften Variable mit dem Drehencoder erhöht oder erniedrigt. Außerdem wird eine Funktion aufgerufen, wenn sich der Wert dieser Variable verändert. Dies wird zum Beispiel bei der Einstellung der maximalen und minimalen Drehzahl der \acp{BLDCMot} verwendet, um den Wert in das Register des jeweiligen Timer Match Registers zu schreiben. Somit kann z.B. die Einstellung der Drehzahlwerte überprüft werden.

\subsection{Aufbau des \aclp{HMI}}
Das \ac{HMI} wird in einem eigenen Task aufgebaut. Beim ersten Durchlauf wird zuallererst das \ac{OLED} sowie die benötigten Menüs initialisiert. Danach werden im Abstand von einer Sekunde zuerst das Logo von \ac{NXP} und danach das Logo der HAW Landshut angezeigt. Nach wiederum einer Sekunde wird der Hauptbildschirm geöffnet. Dort kann mit dem Taster in das Hauptmenü gewechselt und zwischen dem Drive-, Hardware-, Expert-, About- und Hide Menü gewählt werden. Aus zeitlichen Gründen sind nur das Hardware und Hide Menü implementiert. Das Hide Menü wechselt lediglich vom Hauptmenü zurück auf den Hauptbildschirm.\vspace{11pt}
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

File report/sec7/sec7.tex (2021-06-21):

%*****************************************************************
%*************************** Section 7 ***************************
%**************** Streckenerkennung des Fahrzeugs ****************
%*****************************************************************

\pagestyle{fancy}
\rhead{\thepage} \chead{} \lhead{\ref{Sec7}. \nameref{Sec7}}
\cfoot{}

\section{Streckenerkennung des Fahrzeugs}\label{Sec7}
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

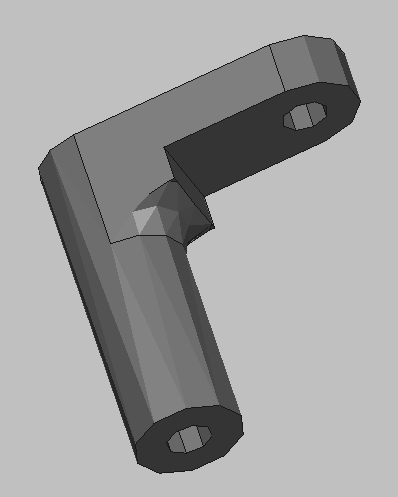
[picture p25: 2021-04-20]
report/sec2/images/3DAnbaukomponenten/Konstruktionsbilder/PlatinenHalterungenKonstruktion.png

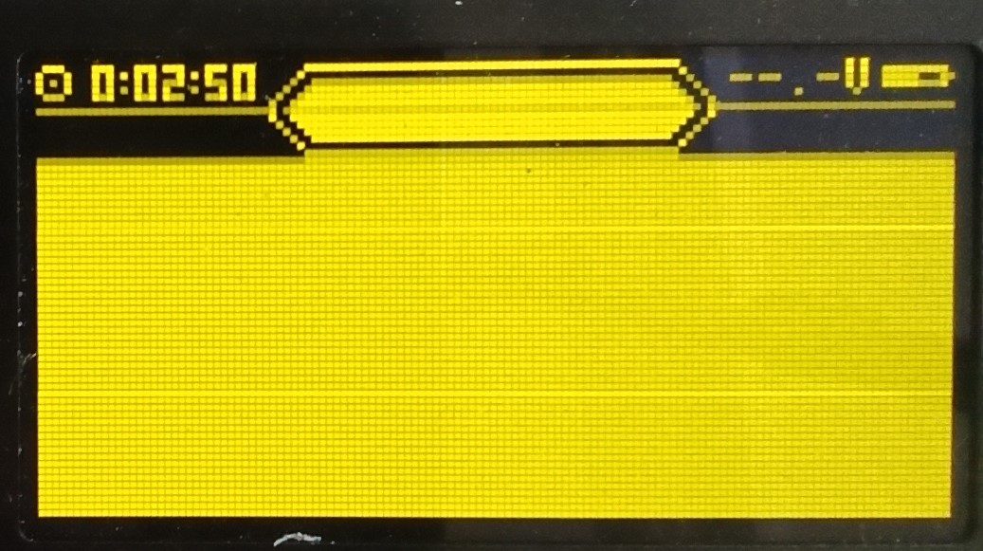
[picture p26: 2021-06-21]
report/sec6/images/funcPage.jpg

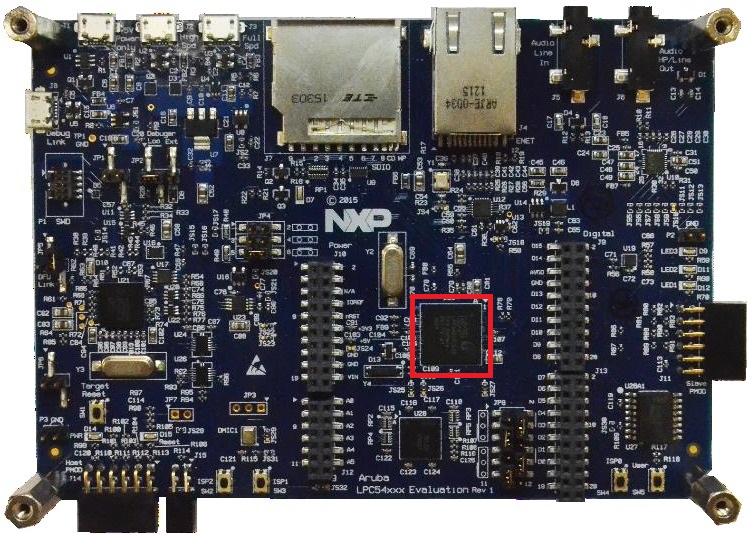
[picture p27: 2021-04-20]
report/sec3/images/Controllerplatine.jpeg

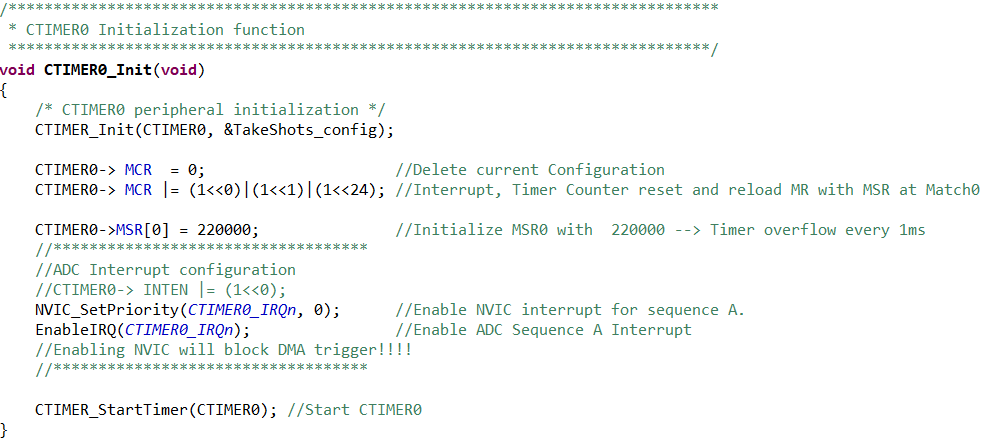
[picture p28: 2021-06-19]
report/sec7/images/code/CTIMER0Init.png

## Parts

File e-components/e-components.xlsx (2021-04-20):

Mouser Bestellungen
 | Drehzahlmessung: | Fertig
Menge: | Bauteil: | Artikelnummer Mouser: | Zusatzinformationen | Einzelpreis (1St.)
8x | 1kΩ Metallschichtwiderstand | 660-MF1/4DCT26A1001F | 250mW 1% | 0.101 € | bedrahtet
0x | 47kΩ Metallschichtwiderstand | 603-MFR-25FTE52-47K | 250mW 1% | 0.093 € | bedrahtet
4x | 100kΩ Potentiometer | 652-PTV09A-4025UA104 | 50mW | 0.686 € | bedrahtet
4x | 10kΩ Metallschichtwiderstand | 660-MFS1/4DCT52A1002 | 250mW 1% | 0.101 € | bedrahtet
2x | Operationsverstärker | 926-LM358AN/NOPB |  | 0.872 € | bedrahtet
4x | 0.33μF Keramikvielschichtkondensator | 581-SR205E334MART | 2.54mm Leiterabstand | 0.381 € | bedrahtet
4x | 0.1μF Keramikvielschichtkondensator | 581-SR155E104M | 2.54mm Leiterabstand | 0.432 € | bedrahtet
 | Bedienungs-Board: | Fertig
Menge: | Bauteil: | Artikelnummer Mouser: | Zusatzinformationen | Einzelpreis (1St.)
1x | Drehencoder | 652-PEC12R-4220F-S24 |  | 0.949 € | bedrahtet
1x | Piezo-Summer | 490-CMI-1295-0585T |  | 0.991 € | bedrahtet
 | Verteilerplatine: | Fertig
Menge: | Bauteil: | Artikelnummer Mouser: | Zusatzinformationen | Einzelpreis (1St.)
1x | 0.33μF Keramikvielschichtkondensator | 581-SR205E334MART | 2.54mm Leiterabstand | 0.381 € | bedrahtet
2x | 0.1μF Keramikvielschichtkondensator | 581-SR155E104M | 2.54mm Leiterabstand | 0.432 € | bedrahtet
1x | Linearspannungsregler | 511-L7805CV | Für Controller-Versorgungsspannung | 0.440 € | bedrahtet
1x | USB-Stecker | 806-KUSBX-AS1N-B | Für Controller-Versorgungsspannung | 0,508 € | bedrahtet
 | Steckverbinder: | Fertig
Menge: | Bauteil: | Artikelnummer Mouser: | Zusatzinformationen | Einzelpreis (1St.)
5x | Buchsenleiste 2x10 SMD | 200-SSM110LDV |  | 3.050 € | SMD
5x | Buchsenleiste 2x6 SMD | 200-SSM106LDV |  | 2.290 € | SMD
2x | Flachbandkabel | 200-IDSS10D1200G |  | 6.530 €
 | Allgemeines: | Noch nicht fertig!
Menge: | Bauteil: | Artikelnummer Mouser: | Zusatzinformationen | Einzelpreis (1St.)
?x | Stiftleiste 1x10 | 538-90120-0130 | 2.54mm Abstand, Breakaway, Tin | 0.872 €
?x | Stiftleiste 2x10 | 538-10-97-7105 | 2.54mm Abstand, Breakaway, Tin | 0.830 €
?x | Buchsenleiste 1x3 | 538-90147-1103 | 2.54mm, Gold | 0.762 €
?x | Buchsenleiste 1x4 | 538-90147-1104 | 2.54mm, Gold | 1.240 €
?x | Buchsenleiste 1x6 | 538-90147-1106 | 2.54mm, Gold | 1,58 €
?x | Buchsenleiste 1x8 | 538-90147-1108 | 2.54mm, Gold | 2.070 €
?x | Buchsenleiste 1x10 | 538-90147-1110 | 2.54mm, Gold | 2.140 €
?x | Buchsenleiste 2x4 | 538-90151-2104 | 2.54mm, Gold | 1.150 €
?x | Buchsenleiste 2x6 | 538-90151-2106 | 2.54mm, Gold | 3.240 €
?x | Buchsenleiste 2x8
?x | Buchsenleiste 2x10 | 538-90151-2110 | 2.54mm, Gold | 2.190 €
?x | Stiftleiste abgewinkelt 1x10 | 538-90121-0130 | 2.54mm, tin | 0.999 €
?x | Stiftleiste abgewinkelt 2x10 | 538-90122-0125 | 2.54mm, Tin | 1.330 €
Conrad Bestellungen
 | Servo-Lenkung: | Fertig
Menge: | Bauteil: | Artikelnummer Conrad: | Zusatzinformationen | Einzelpreis (1St.)
1x | Schalt-Spannungsregler | 1435725 - NA | Spannungsversorgung Servo | 16.990 €

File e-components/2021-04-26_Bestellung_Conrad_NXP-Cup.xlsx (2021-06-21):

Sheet: Bestellschein
 |  |  |  |  |  | HOCHSCHULE FÜR ANGEWANDTE WISSENSCHAFTEN LANDSHUT
HOCHSCHULE LANDSHUT | Am Lurzenhof 1 | D-84036 Landshut | Germany |  |  |  |  |  |  | ABTEILUNG Service Finanzen
Conrad Electronic SE Klaus-Conrad-Straße 1 92240 Hirschau webmaster@conrad.de |  |  |  |  |  |  | Am Lurzenhof 1 D-84036 Landshut Tel. +49 (0)871 – 506 0 Fax +49 (0)871 – 506 506 finanzen@haw-landshut.de www.haw-landshut.de
 |  |  |  |  |  |  | DATUM
 |  |  |  |  |  |  | 2021-04-26
Bestellnummer |  |  |  |  |  | Kundennummer
 |  |  |  |  |  | 48648475
Bestellung
Folgende Gegenstände und / oder Leistungen sind gemäß den Auftragsbedingungen der Hochschule Landshut zu liefern bzw. zu erbringen:
Pos. | Beschreibung: |  |  |  |  | Bestell Nr. | Menge | Stückpreis in € brutto | Betrag in € brutto
1 | Master BEC BOY BEC-Spannungsregler 5 - 25 V 3 A |  |  |  |  | 1435725 - NA | 1 | 14.95 | 14.95
2 | econ connect Buchsenleiste, Reihen: 2, Polzahl je Reihe: 10, BLG2X10 |  |  |  |  | 1492267 - YD | 10 | 0.39 | 3.90
3 | Connfly Stiftleiste (Standard) Anzahl Reihen: 1 Polzahl je Reihe: 10 |  |  |  |  | 1390100 - YD | 20 | 0.17 | 3.40
4 | Würth Elektronik Stiftleiste, Anzahl Reihen: 2 Polzahl je Reihe: 6 |  |  |  |  | 1898789 - YD | 25 | 0.49 | 12.25
5 | USB-Steckverbinder 2.0 - Ultra-Flach Stecker, Einbau TC-A-USB |  |  |  |  | 1586518 - YD | 1 | 0.79 | 0.79
6 | STMicroelectronics L7805CV-DG Spannungsregler, TO-220, 5V, 1.5 A |  |  |  |  | 1184697 - YD | 1 | 0.73 | 0.73
7 | 93038c213a Miniatur Summer Geräusch-Entwicklung: 85 dB Spannung: 5 V |  |  |  |  | 1511468 - YD | 1 | 0.64 | 0.64
8 | Fischer Elektronik Buchsenleiste, Reihen: 1, Polzahl: 36, trennbar |  |  |  |  | 736765 - YD | 5 | 2.84 | 14.20
9 | econ connect Buchsenleiste, Reihen: 2, Polzahl je Reihe: 6, BLG2X6 |  |  |  |  | 1492296 - YD | 10 | 0.23 | 2.30
 |  |  |  |  |  |  |  |  | 0.00
 |  |  |  |  |  |  |  |  | 0.00
 |  |  |  |  |  |  |  |  | 0.00
 |  |  |  |  |  |  |  |  | 0.00
 |  |  |  |  |  |  |  |  | 0.00
 |  |  |  |  |  |  |  |  | 0.00
 |  |  |  |  |  | Gesamtpreis (brutto) |  |  | 53.16
 |  |  |  |  |  | Versand (brutto) |  |  | 0.00
 |  |  |  |  |  | USt.* |  | 0 % | 0.00
 |  |  |  |  |  | Gesamtpreis (brutto) |  |  | 53.16
Um Rückfragen bzw. Falschlieferungen auszuschließen bitten wir Sie, folgende Punkte zu beachten:
1. Auf allen Zuschriften (Lieferscheinen / Rechnungen etc.) ist unsere Bestellnummer anzugeben. 2. Bei Aufträgen, die mehrere Einheiten umfassen ist der Auftragnehmer nicht berechtigt nach Teillieferungen / -leistungen Rechnung zu legen.
3. Versand- und Lieferanschrift: |  |  |  | Hochschule Landshut, Am Lurzenhof 1, 84036 Landshut
Mit freundlichen Grüßen
____________________________________ |  |  |  |  |  | ____________________________________
Unterschrift Service Finanzen |  |  |  |  |  | Unterschrift Budgetverantwortlicher
 | Zahlungen an die Staatsoberkasse Bayern | Vermerk: Hochschule Landshut Bayerische Landesbank München | IBAN: DE75 7005 0000 0001 1903 15 | BIC: BYLADEMM Steuernummer: 132/114/20760 | Ust-IdNr: DE 811 335 517
Begründung der Beschaffungsmaßnahme:
1. | Beschaffung für: |  |  | Fakultät Elektrotechnik und Wirtschaftsingenieurwesen / Digitaltechnik >RSH< / K0 01
 |  |  |  | (Fakultät / Organisationseinheit / Raum-Nr.)
2. | Gefahrstoff
 | S | nein
 | £ | ja, Datenblatt liegt ausgefüllt bei.
3. | Angaben zur Art der Auftragsvergabe
3.1 | Freihändige Vergabe / Beschränkte Ausschreibung (Auftragswert unter 50.000 € netto)
 | Die Auftragserteilung erfolgt nach folgenden Kriterien:
 | S | bis 1000 € netto - Direktkauf
 | £ | über 1000 € netto: Es wurden mindestens drei schriftliche Angebote/Preisvergleiche eingeholt und liegen der Bestellung bei.
 |  | Der Auftrag wird der Firma erteilt, die das preisgünstigste bzw. wirtschaftlichste Angebot abgegeben hat.
 |  | £ | von dem Einholen dreier schriftlicher Angebote oder Preisvergleiche wurde abgesehen – Begründung auf Beiblatt
 |  |  | Firma / Ort: |  | Gesamtpreis netto: | Bemerkungen
 |  | 1.
 |  | 2.
 |  | 3.
 | £ | bei Beschränkter Ausschreibung: Leistungsverzeichnis liegt bei.
3.2 | Öffentliche/Beschränkte Ausschreibung (national; Auftragswert ab 50.000 € netto)
 | £ | Leistungsverzeichnis liegt bei. Der Ablauf des Verfahrens ist frühzeitig mit dem Service Finanzen abzusprechen!
3.3 | Öffentliche Ausschreibung in der EU (EU-weit; Auftragswert ab 209.000 €)
 | £ | Leistungsverzeichnis liegt bei. Der Ablauf des Verfahrens ist frühzeitig mit dem Service Finanzen abzusprechen!
4. | Inventarisierung
 | (bei Investitionen über 410 Euro netto / Software generell)
 | Gebäude |  |  |  | Raum-Nr. | Zubehör / Erweiterung zu Inv.-Nr.
 | £ |  | Neuanschaffung, Ersatzbeschaffung für verschrottetes Gerät – Wert über 410 €
 | £ |  | Neuanschaffung – Wert bis 410 € - gehört zur Sachgesamtheit
 | S |  | Verbrauchsmaterial
 | £ |  | Reparatur/Wartung
 | £ |  | Software
 | £ |  | Sonstiges
5. | Bestätigung
 | Ich bestätige die Richtigkeit der Angabe und die Beachtung der Vorgaben der VOL/A.
 | 2021-04-26 |  |  |  |  |  |  | Mathias Rausch
 | Datum |  |  |  |  | Unterschrift des / der BestellerIn
6. | Geprüft |  |  |  |  |  | (nur für Fakultäten)
 | Die Mittel stehen zur Verfügung. |  |  |  | 5600 302 |  | TG 73 £ | TG 96 £
 |  |  |  |  | Kostenstelle:
 | Datum |  |  |  |  | Unterschrift des/ der Budgetverantwortlichen
Hinweis: Es können nur vollständig ausgefüllte Bestellungen bearbeitet werden!

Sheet: Bestellschein (Erweiterung)
HOCHSCHULE LANDSHUT | Am Lurzenhof 1 | D-84036 Landshut | Germany |  | HOCHSCHULE FÜR ANGEWANDTE WISSENSCHAFTEN LANDSHUT
 |  |  |  |  | DATUM
Conrad Electronic SE Klaus-Conrad-Straße 1 92240 Hirschau webmaster@conrad.de |  |  |  |  | 2021-04-26
Bestellnummer |  | Kundennummer
0 |  | 48648475
Pos. | Beschreibung: | Bestell Nr. | Menge | Stückpreis in € brutto | Betrag in € brutto
16 |  |  |  |  | 0.00
 |  |  |  |  | 0.00
 |  |  |  |  | 0.00
 |  |  |  |  | 0.00
 |  |  |  |  | 0.00
 |  |  |  |  | 0.00
 |  |  |  |  | 0.00
 |  |  |  |  | 0.00
 |  |  |  |  | 0.00
 |  |  |  |  | 0.00
 |  |  |  |  | 0.00
 |  |  |  |  | 0.00
 |  |  |  |  | 0.00
 |  |  |  |  | 0.00
 |  |  |  |  | 0.00
 |  |  |  |  | 0.00
 |  |  |  |  | 0.00
 |  |  |  |  | 0.00
 |  |  |  |  | 0.00
 |  |  |  |  | 0.00
 |  |  |  |  | 0.00
 |  |  |  |  | 0.00
 |  |  |  |  | 0.00
 |  |  |  |  | 0.00
 |  |  |  |  | 0.00
 |  |  |  |  | 0.00
 |  |  |  |  | 0.00
 |  |  |  |  | 0.00
 |  |  |  |  | 0.00
 |  |  |  |  | 0.00
 |  |  |  |  | 0.00
 |  |  |  |  | 0.00
 |  |  |  |  | 0.00
 |  |  |  |  | 0.00
 |  |  |  |  | 0.00
 |  |  |  |  | 0.00
 |  |  |  |  | 0.00
 |  |  |  |  | 0.00
 |  |  |  |  | 0.00
 |  |  |  |  | 0.00
 |  | Gesamtpreis (brutto) |  |  | 53.16
 |  | Versand (brutto) |  |  | 0.00
 |  | USt.* |  | 0 % | 0.00
Blatt 2 |  | Gesamtpreis (brutto) |  |  | 53.16

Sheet: Lieferanten
Firmenanschrift 1 | Firmenanschrift 2 | Kundennummer
33
ABB Automation Products GmbH Postfach 12 67 63754 Alzenau vzmuc.deapr@de.abb.com | Telefon 06023/92 0 Telefax 06023/92 3300 | 258479700
ACS Control-System GmbH Lauterbachstr. 57 1/2 84307 Eggenfelden info@acs-controlsystem.de | Tel. (08721) 9668-0 Fax. (08721) 9668-30 | D12897
Adam Hall GmbH Daimlerstr. 9 61267 Neu-Anspach mail@adamhall.com | Tel.: (+49) 60 81 / 94 19 0 Fax: (+49) 60 81 / 94 19 1000 | AH0030530
A-Drive Technology GmbH Ziegelhüttenweg 4 65232 Taunusstein info@a-drive.de | Telefon: +49 (0) 6128 / 9755 - 0 Fax: +49 (0) 6128 / 9755 - 55
AEG Industrial Engineering GmbH Hohenzollerndamm 152 14199 Berlin | Tel. : +49(0)30 820 99 490 Fax : +49(0)30 820 99 499
Ahlborn Mess- und Regelungstechnik GmbH Eichenfeldstraße 1-3 83607 Holzkirchen | Telefon +49 8024 3007-0 Fax +49 8024 3007-10 | 40207
Air Liquide Deutschland GmbH Im Lipperfeld 2 46047 Oberhausen | Fon: 0208 / 85 09 - 255 Fax: 0208 / 85 09 - 250
AJ-Medizintechnik GmbH Bubensulz 10 72358 Dormettingen E-Mail info@akku-partner.com | Telefon (+49) 7427 9153301 Fax (+49) 7427 9153304
Akkuplus.de Lohwiese 1 35108 Allendorf [Eder]
Alex Metall und Baustoffhandel GmbH Mühlenstrasse 72 41352 Korschenbroich E-Mail: info@alex-metall.com | Telefon: 02161 99946-00 Telefax: 02161 99946-11
Allmeson GmbH Ottostraße 9-11 63150 Heusenstamm info@allmeson.de | Tel: +49 (0)6104 405980 Fax: +49 (0)6104 405990 | 20555
ALTERNATE GmbH Philipp-Reis-Str. 9 35440 Linden | Tel.: 06403 - 90 50 37 60 Fax: 06403 - 90 50 37 69 | 20079656
Aluminium-Online-Shop.de Albertusstraße 9 15745 Wildau E-Mail: info@aluminium-online-shop.de | Tel.: 03375 21761 33 Fax: 03375 21761 22
Andreas Hettich GmbH & Co.KG Föhrenstr. 12 D-78532 Tüttlingen Monika.Schrenk@hettichlab.com |  | 116616
Apotheke am Kaserneneck Ritter-von-Schoch-Str.21a 84036 Landshut | Tel:0871-50246
Arndt GmbH & Co. KG Oskar-von-Miller-Straße 6 84051 Essenbach | Telefon:08703 93140
ARP DATACON GmbH Waldstrasse 23 63128 Dietzenbach | Fon: +49 6074 491 100 Fax: +49 6074 491 111 | 2020761
AUCOSYS e. K. Hofhalde 12 73035 Göppigen | Fax: 07161 922 164 Fon: 07161 503 11 48 | 601
Automatic Systeme GmbH Welser Strasse 5 81373 München robfix@automatic-systeme.de | Fon: 089 72 60 93-13 Fax: 089 72 60 93-20 | 10092
autoVimation GmbH Römerweg 1, 76287 Rheinstetten | Phone: +49 (0) 721 6276756
BEZET-WERK GmbH Nahmitzer Damm 30 12277 Berlin | Tel. +49 (0)30-723 87-184 Fax. +49 (0)30-723 87-702
Bio-Rad Laboratories GmbH Heidemannstr. 164 80901 München orders.central.europe@bio-rad.com | Phone: +49 8931884393 Fax: +49 8931884324 | 1048394
Blickle Räder+Rollen GmbH u. Co. KG Heinrich-Blickle-Str. 1 72348 Rosenfeld info@blickle.com | Telefon: +49 7428 932-0 Telefax: +49 7428 932-209 | 3033677
Blue Mountain Spirit Bergschule Keltenweg 2 D 83131 Nußdorf a. Inn info@bluemountainspirit-bergschule.de | Tel: 0049 (0) 8034 705 64 64 Mobil: 0049 (0) 151 1673 6074 Fax: 0049 (0) 8034/ 709 86 69 www.bluemountainspirit-bergschule.de
Breuell & Hilgenfeldt GmbH ebmpapst Service-Center Postfach 2002 22810 Norderstedt info@bh-gmbh.com | Telefon: +49 (0) 40 53 80 92 - 20 Fax: +49 (0) 40 53 80 92 - 84 | 119999
Bürkert GmbH Elsenheimer Strasse 47 80687 München | Fon: 089-829228-0 Fax: 089-829228-50
Bürklin OHG Grünwalder Weg 30 82041 Oberhaching info@buerklin.de | Telefax: (089) 55 875-421 | 0020269
Carl Roth GmbH Schoemperlstr. 3-5 D-76185 Karlsruhe E-Mail: bestellungen@carlroth.de |  | HOCHLAN1
celexon Germany GmbH & Co.KG Gutenbergstr. 2 48282 Emsdetten | Telefon: 0257292391-2216 Fax: 0257292391-2299
Christ-Elektronik GmbH Alpenstraße 34 87700 Memmingen info@christ-elektronik.de | Telefon: +49 83 31 83 71 0 Telefax: +49 83 31 8371 99
Christian Haßler Amselweg 3 83052 Bruckmühl info@outlet76.de | Telefon: 0160-1828691 Telefax: 08062-725976
Conrad Electronic SE Klaus-Conrad-Straße 1 92240 Hirschau webmaster@conrad.de | Tel.: 09622 / 30 - 0 Fax: 0180 5 312110 | 48648475
Consolar Solare Energiesysteme GmbH Strubbergstraße 70 60489 Frankfurt a. M. | Tel.: +49 (0) 69 - 74 09 328 - 0 Fax: +49 (0) 69 - 74 09 328 - 55 | 11999
Cyberport GmbH Postfach 10 11 41 01081 Dresden E-Mail: geschaeftskunden@cyberport.de | Tel.: +49 351 3395-7000 Fax: +49 351 3395-849
Dastex Reinraumzubehör GmbH & Co. KG Draisstr. 23 76461 Muggensturm Email: info@dastex.com | Telefon +49 (0) 7222 - 96 96-60 Telefax +49 (0) 7222 - 96 96-88
dataTec AG Ferdinand-Lassalle-Str. 52 72770 Reutlingen Fax: 0 71 21 - 51 50 10 info@datatec.de | Tel.: 0 71 21 - 51 50 50 | D007520
DELTA-V GmbH Eichenhofer Weg 71 42279 Wuppertal info@delta-v.de | Fon: 0 23 39 / 90 98 50 Fax: 0 23 39 / 90 95 01 | 500122
DEUTRONIC ELEKTRONIK GmbH Deutronicstr. 5 84166 Adlkofen sales@deutronic.com | Tel: +49 8707 920199 Fax: +49 8707 1004 | 10445
Diesner AG Paul-Klee-Strasse 32 84034 Landshut info@Laser-Technik.de | Telefon: +49 871 65336 Telefax: +49 871 65337 | K 9999
Digi-Key 701 Brooks Avenue South Thief River Falls MN 56701 USA eu.support@digikey.com | Fax: +31 (0)53 484 9583 | 1085132
Distrelec Schuricht GmbH Lise-Meitner-Str. 4 28359 Bremen verkauf@distrelec.de | Phone: 0421 3654 200 Fax: 0421 3654 236
Dr. Fritz Faulhaber GmbH & Co. KG Antriebssysteme Daimlerstrasse 23/25 71101 Schönaich info@faulhaber.com | Telefon: +49 (0) 7031 / 638 - 0 Fax: +49 (0) 7031 / 638 - 100 | 36633
DREKO-WERBUNG GbR Gubener Strasse 25 15907 Lübben info@dreko-werbung.de | Telefon: 03546-229960 Fax: 03546-2296961 | 3304
E. Kretzschmar GmbH Alte Schulstrasse 32 51515 Kürten-Bechen | Fon: 02207 709-0 Fax: 02207 6713 | 15185
EA Elektro-Automatik GmbH & Co.KG Setzbergstrasse 4 83679 Sachsenkam ea-sued@elektroautomatik.de | Tel. : (08021) 905 000 Fax : (08021) 905 002 | 19250
ebm-papst Landshut GmbH Hofmark-Aich-Str. 25 84030 Landshut info3@de.ebmpapst.com | Fax. 0871 1 43 90 59
EBV Elektronik GmbH & Co KG Im Technologiepark 2-8 85586 Poing | Telefon: +49 (0) 8121 / 774 - 0 Fax: +49 (0) 8121 / 774 - 422
ECA Fodermayrstr. 24 80993 München info@eca.de | Tel.: 089 13 40 04 Fax: 089 16 62 31 | 90483
Edmund Optics GmbH Deutschland Zur Giesserei 8 76227 Karlsruhe | Telefon: +49 721 627 37 30
Edmund Optics GmbH Isaac-Fulda-Allee 5 52124 Mainz sales@edmundoptics.de | Tel: 06131/57 00 0
efa&käufl Liebigstr.3 84030 Landshut info@efa-kaeufl.de | Telefon: 0871/962250 Fax: 0871/9622514
EFG-Gienger KG Gartenstraße 1 84030 Ergolding michael.kuester@gc-gruppe.de | Fon 0871 96 66 - 0 Herr Küster Fon 0871 96 66 - 32 | FALA02
Elektronik-Kontor Messtechnik GmbH Postfach 1642 74006 Heilbronn mess@ekomess.de | Tel. 07131 89829-0 Fax: 07131 89829-13 | 26790
EMCOM GmbH Lessingstr. 49 47799 Krefeld eMail: info@akku500.de | Telefon: 02151 501600 Telefax: 02151 501601 | 1328505
EMM SERVICE GmbH Blücherstraße 24 06120 Halle E-Mail: info@elektromotorenmarkt.de | Telefon: +49 (0)345 68 243 70 Telefax: +49 (0)345 68 243 71
EMS Elektromotoren GmbH Gewerbegebiet - Egelsee 13 93353 Siegenburg | Telefon 09 444 / 976-0 Telefax 09 444 / 976-177
ENERGIEWENDE Verlag & Vertrieb Sägewerkstr. 3 83395 Freilassing service@solarshop.net | Tel.: 08654 - 77 1 889 Fax: 08654 - 77 1 890
Engelbert Strauss GmbH &Co.KG Frankfurter Straße 98-102 63599 Biebergmünd | Telefon 06050 971012 Telefax 06050 971090
Epoxy Produkte GmbH Kalbensteinberg 57 91720 Absberg hs@epoxy-produkte.de | Telefon: 09837/976693 Fax: 09837/976699 | 1649
Erich Grau GmbH Stanzwerk Uhlandstraße 3-7 74372 Sersheim | Telefon: 07042 / 8363-21 Telefax: 07042 / 8363-33 | 699 035
Erwin REUMÜLLER TEWA Elektromotoren Ges.mbH Johann Josef Krätzergasse 6 A-1230 Wien reuli@reumueller-tewa.at | Tel: +43 1 865 92 60 – 0 Fax: +43 1 869 83 18 | 29758
Farnell GmbH Keltenring 14 82041 Oberhaching verkauf@farnell.com | Telefon: +49 89 61 30 30 Fax: +49 89 61 30 33 51 | 701066
FeatherLight B.V. Stationsweg 41 3331 LR Zwijndrecht (Niederlande) E-Mail: info@gasfedershop.de | Telefon: +31 78 204 9322
Fedotec GbR Murgtalstraße 28, D-79736 Rickenbach | Phone: +49(0) 7765 96590
FEGA & Schmitt Landshut Elektrogroßhandel GmbH Ludmillastraße 30 84034 Landshut landshut@fega-schmitt.de | Tel.: +49 871 92290-0 Fax: +49 871 92290-33 | 1744061701
Fischer Oberflächentechnik GmbH Wullener Feld 15a 58454 Witten info@fot.de | Telefon: (023 02) 2 82 55-0 | 1779
Fluke Deutschland GmbH Service und DKD Kalibrierlabor Heinrich-Pesch-Straße 9-11 50739 Köln service.de@fluke.com | Tel: +49 (0)69 2222 20 210 Fax: +49 (0)69 2222 20 211 | 4149126
FLYERALARM GmbH Postfach 55 69 97005 Würzburg
Forster Reinhold Schreinerei Eugenbacher Str. 13 84032 Altdorf | Fon: 0871 3 22 51 Fax: 0871 3 49 25 Mobil: 0179 46 18 37 4
FORUM VERLAG HERKERT GMBH Mandichostraße 18 86504 Merching service@forum-verlag.com | Telefon: +49 (0)8233 381-123 Telefax: +49 (0)8233 381-222
Frantos GmbH & Co KG Friedrich-Schüle-Str. 15 85622 Feldkirchen bei München E-Mail: shop@frantos.com | Telefon: +49 / 89 / 6389308-0 Telefax: +49 / 89 / 6389308-29
Gaerner GmbH Ruhrorter Str. 195 47119 Duisburg service@gaerner.de | Telefon +49 (0) 203 / 8094-0 Telefax +49 (0) 203 / 8094-4215 | 0820405
GE Sensing & Inspection Technologies GmbH Niels- Bohr - Straße 7 31515 Wunstorf E- Mail: service.phoenix@ge.com | Telefon: 05031-1720 Fax: 05031-9179446
Gebrüder Recknagel Präzisionsstahl GmbH Metzelser Str. 21-25 98547 Christes grp@stahlnetz.de | Telefon: +49 36844 480-0 Telefax: +49 36844 480-55
Gehmeyr GmbH & Co. KG, Techn. Vertrieb Auerbacher Straße 2 93057 Regensburg info@gehmeyr.de | Fon: 0941 696 81-0 Fax: 0941 696 81-49 | 47036
General Elektronik GmbH Am Stadtweg 3 39167 Hohendodeleben | Fon: +49 39204 796-0
Gerhard Mann GmbH & Co. KG Postfach 1592 84003 Landshut | Fon: 0871 70 01-0 Fax: 0871 70 01-40 | FALA01
Gerhard Schützinger Labor-Schütz GmbH Eichwiesenring 6 70567 Stuttgart | Fon: +49 (0)711-715 46-0 Fax: +49 (0)711-715 46-40
Giseke GmbH & Co. KG Pankstraße 8-10 13127 Berlin service@akku.net | Fon: +49 (030) 42410690 Fax: +49 (030) 42804950 | 31657
GMC-I SERVICE GmbH Beuthener Str. 41 90471 Nürnberg service@gossenmetrawatt.com | Fon: 0911 8602 - 0 Fon Kal.-Service: 0911 8177180 Fax: 0911 8602 - 669 | 017147
GOSSEN Foto- und Lichtmesstechnik GmbH Lina-Ammon-Str. 22 90471 Nürnberg stephan.frahnert@gossen-photo.de | Tel.: +49 911 86 02 181 Fax: +49 911 86 02 142
Gras Maschinenbau GmbH Hirschlandstrasse 18 73730 Esslingen | Fax: 0711 318 359 Fon: 0711 312 854 | D35122
GRONARD Metallbau & Stadtmobiliar GmbH Bayerwaldstraße 23 81737 München | Tel: +49 (0) 89.670 10 15 Fax: +49 (0) 89.637 61 71
H&S Kunststofftechnik GmbH Charlottenhütte 2 57080 Siegen info@hs-kunststoffe.de | Telefon: 0271/35954-0 Fax: 0271/3595499 | D/176797
H. Gautzsch Großhandel Bayern GmbH & Co. KG Edisonstr. 13 84453 Mühldorf Wolfgang.Bichlmaier@GautzschBayern.de | Telefon-Nr. 08631/16752166 Fax-Nr. 08631/16752199 | 5362
Hadersdorfer Reisen Moosburg GmbH & Co. KG Neue Industriestr. 12 85368 Moosburg | Tel.: 08761 - 66 99 12 Fax: 08761 - 66 99 33
Hagemeyer Deutschland GmbH & Co. KG Ottostraße 16 a 84030 Landshut info.landshut@hagemeyerce.com | Tel.: 0871 974826-0 Fax: 0871 974826-10 | 104030
Hans-Erich Gemmel & Co. GmbH Industriestraße 5 90765 Fürth info@gemmel-metalle.de | Tel: +49 911/ 93 61 66 Fax: +49 911/ 936 16 78 | 425754
HARTMETALLWERKZEUGFABRIK ANDREAS MAIER GMBH Stegwiesen 2 88477 Schwendi-Hörenhausen | Tel: 07347/61-137 Fax: 07347/61-141 | 206660
Hausverwaltung - im Haus -
Heinz Büchner Elektronik Greifenhager Str. 22 10437 Berlin | Tel. 030 447 15181 Fax. 030 44 71 51 82
Herbert Waldmann GmbH & Co. KG Peter-Henlein-Straße 5 78056 VILLINGEN-SCHWENNINGEN info@waldmann.com | Tel.: +49 7720 601 0 Fax: +49 7720 601 290 | 1075902
Hermann Adam & Co. KG Felix-Wankel-Strasse 1 85221 Dachau marianne.rummel@adam-gmbh.de | Fon: 08131 28 08 - 0 Fax: 08131 2808 - 59 Fon: 08131 28 08 - 51
Hilti Center Landshut Industriestrasse 11 84030 Ergolding de.Kundenservice@Hilti.com | Telefon: 0871 / 9753610 Fax: 0871 / 9753611 | 0010392598
Hoffmann GmbH Qualitätswerkzeuge Haberlandstraße 55 81241 München info@hoffmann-group.com | Fon: 089 83 91-0 Fax: 089 83 91-89 | 1348346
HUG Industrietechnik und Arbeitssicherheit GmbH Am Industriegleis 7 84030 Ergolding verkauf@hug-technik.com | Fon: 0871 / 97 410 - 0 Fax 0871 / 97 410 - 55 | 120101
Hugo Huber Kälte- und Klimaanlagen Gabelsbergerstr. 59 84034 Landshut | Tel. 0871 - 6 90 85 Fax 0871 - 6 30 33 9 Mobil: 0172 - 620 11 54
IBS Magnet Ing. K.-H. Schroeter Kurfürstenstrasse 92 12105 Berlin | Tel +49 (0)30 706 30 05 Fax +49 (0)30 802 20 94
Idel Versandhandel GmbH Osterbrooksweg 83 22869 Schenefeld service@kabeldirekt-shop.de | Telefon: 040 537997410 Telefax: 040 537997414
IDS Imaging Development Systems GmbH Dimbacher Strasse 6-8 74182 Obersulm info@ids-imaging.de | Telefon: +49 (0) 7134 / 96196-0 Fax: +49 (0) 7134 / 96196-99 | D015784
ifm electronic gmbh Niederlassung Bayern Boschstraße 1 82178 Puchheim info.ifm.com | Telefon: 089/80091-0 Fax: 089/80091-11 | 5015217
IKARUS Solarsysteme GmbH Dieselstr. 45 87437 Kempten info@ikarus-solar.de | Fon: +49 831 575000 u. +49 (0)831 52387070 Fax: +49 831 5750040 u. +49 (0)831 523870740 | 11376
INNO-Systems Handels GMBH Hohenbruckstraße 8 90425 Nürnberg inno-systems@ipz-group.com | Fon: +49 911 955 1790 Fax: +49 911 955 17938 | 14425
IPC-Computer Deutschland GmbH Hauptstraße 37 D-77960 Seelbach info@ipc-computer.de | Telefon: +49 (0) 7823 96 123 - 0 Telefax: +49 (0) 7823 96 123 - 21
isel Germany AG Untere Röde 2 36466 Dermbach | Telefon +49 6659981773 Telefax +49 6659981777 | 301629
ITHaus UG (haftungsbeschränkt) Hammerbach 7 83229 Aschau Bayern | Telefon: 080526779402
JAERA GmbH & Co. KG Greifswalder Straße 2 D-30880 Laatzen / Deutschland info@jaera.de | Telefon: +49 / (0) 5102 / 9196-0 Telefax: +49 / (0) 5102 / 9196-20 | 151474
Jäger Messtechnik Rheinstraße 2-4 64653 Lorsch info@adwin.de | Tel +49 6251 9632-0 Fax +49 6251 56819
JU-Gruppe Landauerstr. 14, 21-23 D-74582 Gerabronn schnelldienst@ju-briefkasten.de | Telefon: +49 (0) 7952 6030 Telefax: +49 (0) 7952 603-102 E-Mail: info@ju-online.de
Jungheinrich PROFISHOP AG & Co. KG Haferweg 24 22769 Hamburg info@jh-profishop.de | Tel: +49 40 89706-0 Fax: +49 40 89706-111 | 211148505
KAISER+KRAFT GmbH Presselstr. 12 70191 Stuttgart service@kaiserkraft.de | Telefon +49 (0) 711 / 3465 - 60 Telefax +49 (0) 711 / 3465 - 6100 | 0064494
Karlsruher Glastechnisches Werk Gablonzerstrasse 6 76185 Karlsruhe info@kgw-isotherm.de | Fon: 0721 / 95 89 7 - 0 Fax: 0721 / 95 89 7 - 77
KELLER Gesellschaft für Druckmesstechnik mbH Schwarzwaldstr. 17 D 79798 Jestetten | Tel. 07745 - 9214 0 Fax 07745 - 9214 50 | 37371
Kemmerich Elektromotoren GmbH & Co. KG Hückeswagenerstr. 120a 51647 Gummersbach | Telefon +49/ (0) 2261/50198-0 Telefax +49/ (0) 2261/50198-20 | 07039
Kleebauer Elektro Steckengasse 305 84028 Landshut | Fon: 0871 2 24 68
KNF Neuberger Alter Weg 3 79112 Freiburg E Mail: info@knf.de | Tel: 07664-59090
KOBOLD Messring GmbH Nordring 22-24 65719 Hofheim / Taunus info.de@kobold.com | Fon: +49 (0) 6192 299-0 Fax: +49 (0) 6192 233-98 | 196722
König GmbH Kunststoffprodukte Zeppelinstraße 14 82205 Gilching verwaltung@koenig-kunststoffe.de | Telefon +49 8105 7727-100 Telefax +49 8105 7727-101
Konrad GmbH & Co. KG Liebigstrasse 9 84030 Landshut | Fax: 0871 973 95 50 | 10434
Kraus & Naimer GmbH Postfach 10 01 24 D-76231 Karlsruhe thomas.lillich@krausnaimer.com | T: +49 721 59 88-0 F: +49 721 59 28 28 info-de@krausnaimer.com
Krüger & Sohn GmbH Robert Bosch Strasse 1 - 3 84030 Landshut | Fax: 0871 7004 - 50 Fon: 0871 7004 - 10 | 70524
KRUSE Sicherheitssysteme GmbH & Co. KG Duvendahl 92 D-21435 Stelle E-Mail: mail@kruse-sicherheit.de | Telefon: 0 41 74 / 592 145 Telefax: 0 41 74 / 592 155
Küblbeck GmbH & Co. KG Liebigstraße 3 84030 Landshut | Fon: 0871 9 75 53 - 0 Fax: 0871 9 75 53 - 20 | 7861061
Kugellager-Express GmbH Grenzweg 14 A 33758 Schloß Holte-Stukenbrock info@kugellager-express.de | Telefon: +49 (0) 5207/92917-0 Telefax: +49 (0) 5207/92917-28
KYOCERA FINECERAMICS GMBH Solar Division Fritz-Müller-Str. 107 73730 Esslingen/Germany solar@kyocera.de | Tel. +49 - (0) 711 - 93934 - 17 Fax. +49 - (0) 711 - 93934 - 50 www.kyocerasolar.de
Laser 2000 GmbH Argelsrieder Feld 14 82234 Wessling info@laser2000.de | Telefon: +49 8153 405 0 Fax: +49 8153 405 33
Laser Components GmbH Werner-von-Siemens-Straße 15 82140 Olching | Tel.: +49 8142 2864 721 Fax: +49 8142 2864 11 | 1009171
LEMO Elektronik GmbH Hanns-Schwindt-Str. 6 81829 München info@lemo.de | Phone: (+49 89) 42 77 03 Fax: (+49 89) 420 21 92 | 188300
Lenze AG Postfach 10 13 52 31763 Hameln | Phone +49 5154 82 0 Fax +49 5154 82 2800
Leybold Didactic GmbH Leyboldstraße 1 50354 Hürth info@leybold-didactic.de | Telefon: +49 2233 604-0 Telefax: +49 2233 604-222 | 51139
Leybold Vakuum GmbH Bonner Straße 498 50968 Köln | Telefon: +49-(0)221-347-1234 Telefax: +49-(0)221-347-1245
LPKF Laser & Electronics AG Osteriede 7 30827 Garbsen | Tel.: +49 (0) 5131 7095-0 Fax: +49 (0) 5131 7095-90
Lucas-Nülle Lehr- und Meßgeräte GmbH Siemensstraße 2 50170 Kerpen-Sindorf | Telefon: 02273 / 567-0 Telefax: 02273 / 567-69 | 45652
Lumiprobe GmbH Feodor-Lynen-Strasse 23 30625 Hannover de@lumiprobe.com | Phone: +49 511 16596811 Fax: +49 511 16596815
M. Carl e.Kfr. Bertold-Brecht-Strasse 60 90471 Nürnberg m.carl@t-online.de | Fon: 0911 8 14 70 21 Fax: 0911 86 48 68 | 03830194
MÄDLER GmbH Tränkestr. 6-8 70597 Stuttgart info@maedler.de | Telefon + 49 711 720 95-0 Telefax + 49 711 720 95-33 | 162152
MAKRA Norbert Kraft GmbH Zillenhardtstraße 29 73037 Göppingen/Voralb info@makra.de | Telefon: +49 (0) 71 61/9 99 09 - 0 Telefax: +49 (0) 71 61/9 99 09 - 99 | 148401
mawi-therm Temperatur-Prozeßtechnik GmbH Hofstraße 23 40789 Monheim am Rhein info@mawi-therm.com | Tel: +49 (0)2173 51094 Fax: +49 (0)2173 58623 | 90541
MBM Maschinenbau Mühldorf GmbH Münchnerstraße 64 84444 Mühldorf am Inn | Tel:08631 / 605-0 Fax: 08631 / 605-500 Internet: www.mbm-gmbh.com | 12286
MediaLas Electronics GmbH Vogtshalde 9 72336 Baling info@medialas.com | Telefon: 07433-90799 0 Telefax: 07433-90799 22
Meilhaus Electronic GmbH Am Sonnenlicht 2 82239 Alling / Germany sales@meilhaus.com | Fon: 08141 5271-0 Fax: 08141 5271-129
metabion international AG Semmelweisstrasse 3 D-82152 Planegg/Steinkirchen mi@metabion.com
MEYER Industrie-Electronic GmbH Carl-Bosch-Straße 8 49525 Lengerich | Tel: 0 54 81 / 93 85-0 Fax: 0 54 81 / 93 85-12
microstaxx GmbH Wilhelm-Kuhnert-Straße 26 81543 München info@microstaxx.de | Fon: +49 - 89 - 48 90 75 - 0 Fax: +49 - 89 - 48 90 75 - 99 | 31105
MIPA Fachmarkt Altdorferstrasse 1 84032 Landshut | Tel: 0871 973 22-0 | 12054
MIRA - ELECTRONIC GdbR Beckschlagergasse 9 90403 Nürnberg | Telefon: 0911 / 55 59 19 Telefax: 0911 / 58 13 41
MISUMI Europa GmbH Katharina-Paulus-Str. 6 65824 Schwalbach am Taunus verkauf@misumi-europe.com | Telefon: +49 6196 7746 0 Telefax: +49 6196 7746 360 | FHFHLA
Most Industrieprodukte Waldweg 11 85461 Grünbach info@most-industrieprodukte.de | Fon: +49 8122 999 83 60 Fax: +49 8122 999 83 66 | 2526
Mouser Electronics Elsenheimerstr. 11 80687 München | Telefon: +49 (0)89 520 462 110 Fax: +49 (0)89 520 462 120
MR Datentechnik Vertriebs- und Service GmbH Friedrich-Bergius Ring 34 97076 Würzburg d.mehring@mr-daten.de | Telefon: +49 (0) 931 / 35960-28 Fax: +49 (0) 931 / 35960-20 | 100537
Multi Printed Circuit Boards Ltd. Brunnthaler Straße 2 85649 Brunnthal – Hofolding | Telefon: +49 (0)8104 628 0 Telefax: +49 (0)8104 628 160
Multi-Bauelemente-Service Vertrieb von elektronischen Bauelementen GmbH Römerstraße 8 85661 Forstinning multi.bauelemente@mbs.to | Telefon: (08121) 2506 - 0 Telefax: (08121) 2506 - 200 | 10956
Multi-Contact Deutschland GmbH Postfach 1606 79551 Weil am Rhein weil@multi-contact.com | Tel. +49/76 21/6 67 - 0 Fax +49/76 21/6 67 - 100
MVA Mess- und VerfahrensTechnik GmbH Am Kirchenhoelzl 7 D 82166 Graefelfing | Fon +49-89-858369-13 Fax +49-89-858369-70 | 7020
MVT - Mess- und Video-Technik Berliner Strasse 12 71272 Renningen info@mv-technik.de | Telefon: +49 (0) 7159 / 4207329 Fax: +49 (0) 7159 / 17562
myToolStore GmbH Wilhelmstraße 78 68799 Reilingen info@mytoolstore.de | Tel.: +49 (0)6205 3103997 Fax: +49 (0)6205 3057629 Web: http://www.mytoolstore.de | 932012
National Instruments Germany GmbH Ganghoferstraße 70b 80339 München michael.bahmer@ni.com | Telefon: +49 (0) 89 / 741 31 30 Fax: +49 (0) 89 / 714 60 35 | 10819725
Newsales - Inh. A. Gruppe Kapellenstr. 9a 30625 Hannover info@elko-verkauf.de | Tel.: 0511-53326-18 Fax: 0511-53326-17
Nordic Panel GmbH Ohle Kamp 5 21684 Stade | Telefon: 04141 / 787 60 -30 Telefax: 04141 / 787 60 -39
norelem Normelemente KG Postfach 1163 71702 Markgröningen info@norelem.de | Verkauf (07145) 206-41 bis 43 Zentrale (07145) 206-0 Telefax (07145) 206-66 www.norelem.de | 127450/82
OBI Markt Landshut Neidenburger Str. 1 84030 Landshut landshut@obi.de | Tel.: 0871 974260
Omnibusse Richard Petz GmbH Opalstraße 30 84032 Altdorf | Telefon 0871 34994 Telefax 0871 31233
Omnibusunternehmen GÜNTER UNGER Eichenstr. 7 + 9 84172 Buch am Erlbach
online-schrauben.de, e.K Am Brögel 21 42285 Wuppertal info@online-schrauben.de | Telefon: 0202 / 28077 - 60 Telefax: 0202 / 28077 - 69 internet: www.online-schrauben.de | 103665
Orientalmotor Schiessstraße 44 40549 Düsseldorf info@orientalmotor.de | Telefon: 0211-52067-00 Telefax: 0211-52067-099 | 5000887
Ostermeier Andreas Groß- und Einzelhandel Schmidgasse 7 84178 Magersdorf r.a.ostermeier@t-online.de | Fon: 08744 519 Fax: 08744 7148
Paulitschek Maschinen- und Warenvertriebsgesellschaft mbH Zeppelinstraße 3 D-89231 Neu-Ulm E-Mail: info@paulimot.de | Telefon: 0731-23232 Fax: 0731-27676
PEAK-System Technik GmbH Hauptgeschäftsstelle Darmstadt Otto-Röhm-Straße 69 64293 Darmstadt E-Mail: order@peak-system.com | Tel.: +49 6151 / 8173-20 http://www.peak-system.com
PHOENIX CONTACT Deutschland GmbH Flachsmarktstraße 8 32825 Blomberg bestellung@phoenixcontact.de | Telefon: +49 5235 312 000 Telefax: +49 5235 312 999 phoenixcontact.de | 311223
PHYWE Systeme GmbH und Co. KG Robert-Bosch-Breite 10 37079 Göttingen info@phywe.de | Telefon: 0551 604 - 0 Fax: 0551 604 - 107 Web: www.phywe.de
PHYWE Systeme GmbH und Co. KG Robert-Bosch-Breite 10 37079 Göttingen | Phone: +49 (0) 551 604 - 0
Pilz GmbH & Co. KG Postfach 1161 73747 Ostfildern info@pilz.de | Tel.: +49 8142 4670-19 Fax: +49 8142 54 54 1 www.pilz.com | 1977836
PINTER Mess- und Regeltechnik GmbH Kraichgaublick 17 74847 Obrigheim peter.schwindt@pinter-gmbh.de | Telefon: +49-6262-92670-75 Fax: +49-6262-92670-9075
R+W Antriebselemente GmbH Alexander-Wiegand-Str. 8 63911 Klingenberg info@rw-kupplungen.de | Telefon: +49-(0)9372-9864-0 Telefax: +49-(0)9372-9864-20 | 36335
Rauschhuber Electronic Postfach 11 16 84004 Landshut | Fon: +49 871 9 73 55-0 Fax: +49 871 9 73 55-18 | 10222
reichelt elektronik GmbH & Co. KG Elektronikring 1 26452 Sande Germany info@reichelt.de | Telefon : 04422/955-333 Fax : 04422/955-111 | 428593
Reimer Armaturen GmbH Am Mohrenshof 6c 28277 Bremen info@armaturenshop.de | Telefon: +49 (421) 2010150 Telefax: +49 (421) 2010151
Re-In Retail International GmbH Nordring 98a 90409 Nürnberg | Telefon: +49 180 5 712271 Fax: +49 180 5 712272 Tel.:0911 32689888 Fax.:0911 32689889 | 131051093
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

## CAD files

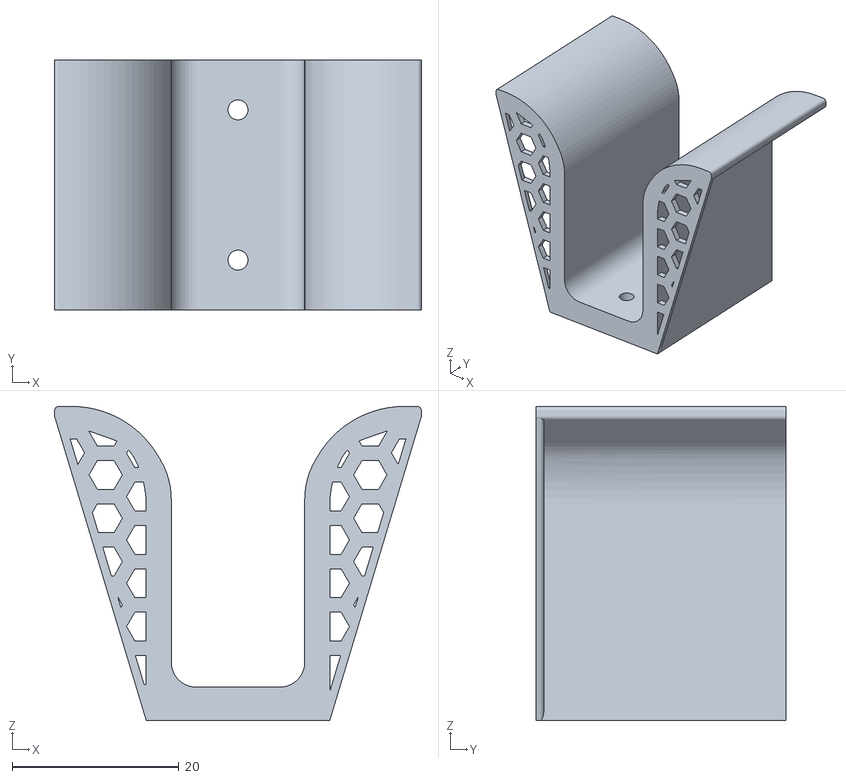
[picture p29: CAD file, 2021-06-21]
3Dprints/Antriebsabdeckung/Antriebsabdeckung v4.stl
44.0 x 30.0 x 37.7

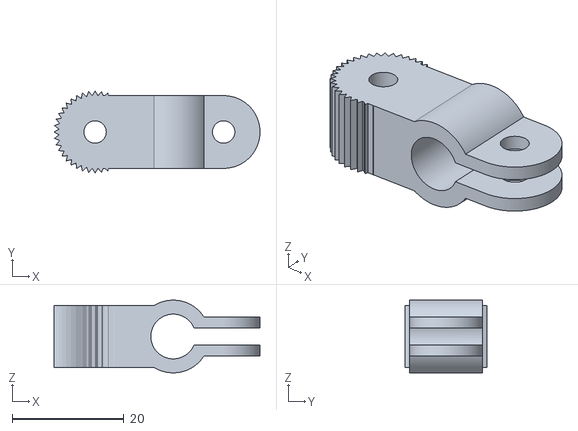
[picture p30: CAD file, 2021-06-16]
3Dprints/Halter Kamera/Halter Kamera/halter_kamera.stl
36.8 x 14.7 x 13.0

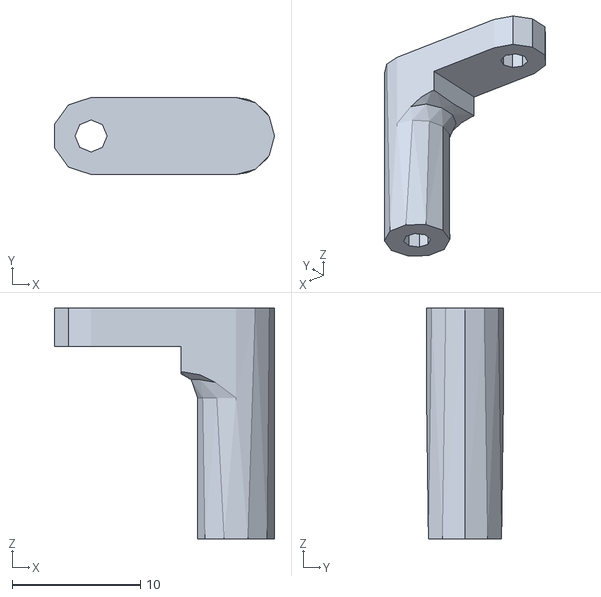
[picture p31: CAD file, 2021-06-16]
3Dprints/Halterung_Platine_einfach.stl
17.2 x 6.00 x 18.0

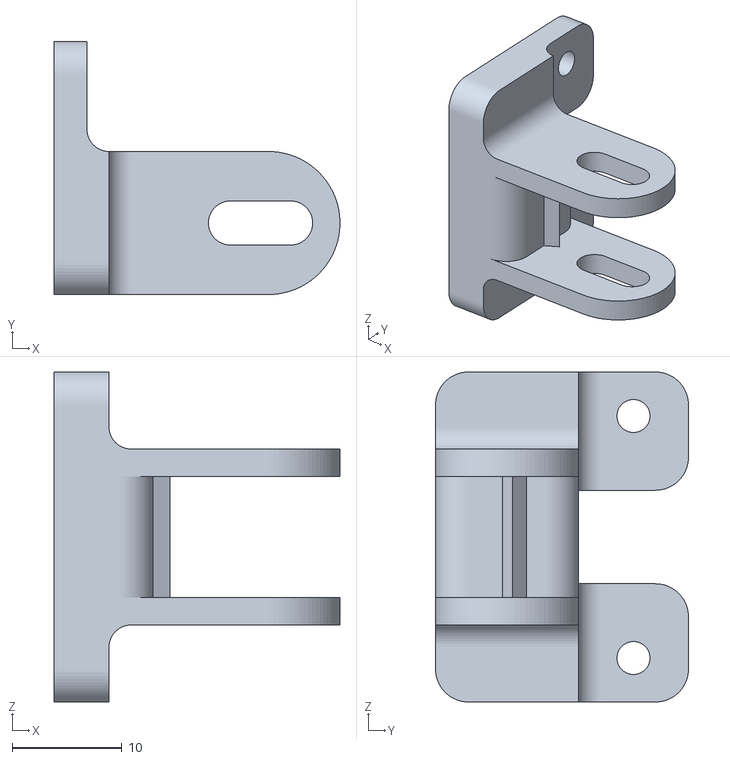
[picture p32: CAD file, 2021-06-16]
3Dprints/Halter Kamera/Halter Kamera/halter_stab.stl
26.0 x 23.0 x 30.0

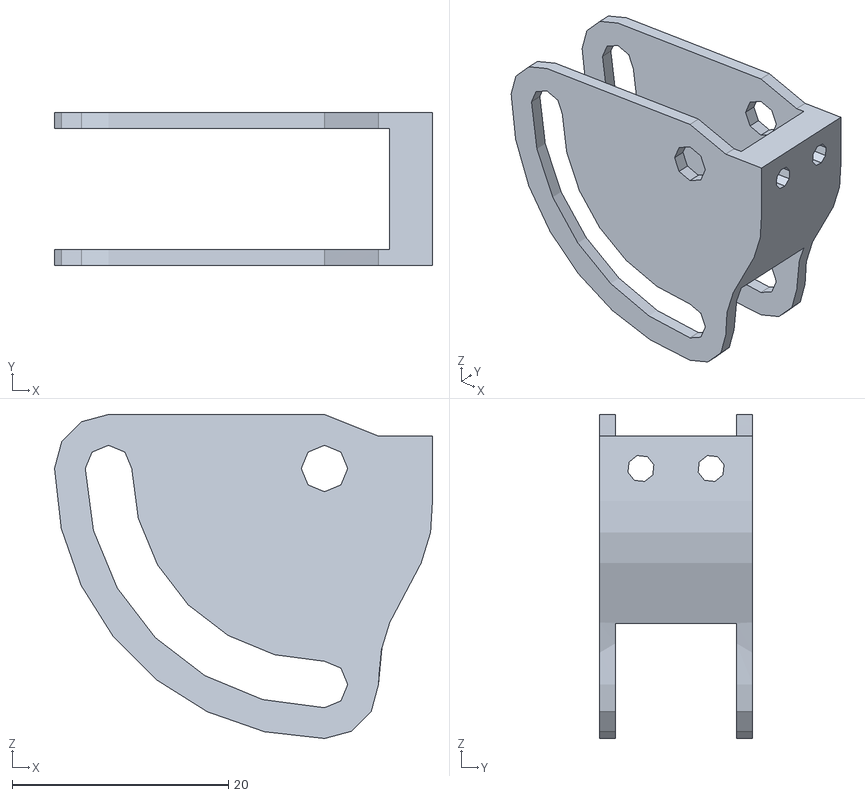
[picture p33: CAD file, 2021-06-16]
3Dprints/project_1277_cad_file_9790531.stl
35.0 x 14.2 x 30.0

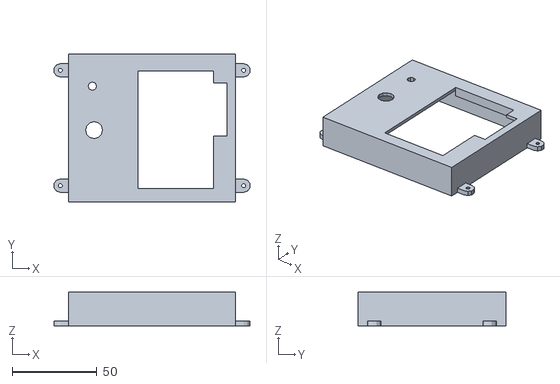
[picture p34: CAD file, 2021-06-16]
3Dprints/Deckel_Display.stl
115.9 x 87.5 x 19.9

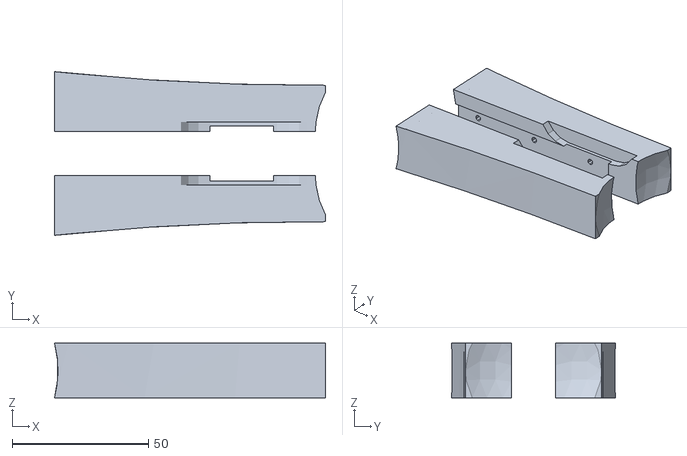
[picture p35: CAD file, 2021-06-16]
3Dprints/Seitenschweller_RechtsUndLinks.stl
99.3 x 60.0 x 20.0

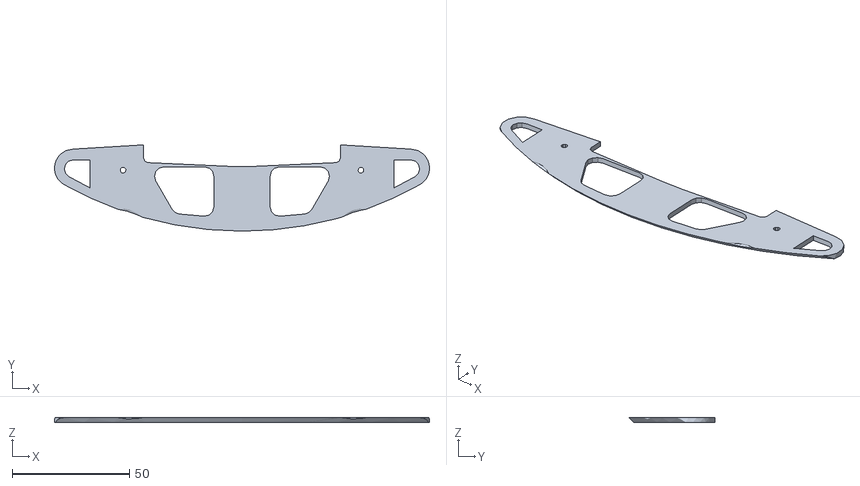
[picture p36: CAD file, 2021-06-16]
3Dprints/Bodenteil_Stoßstange.stl
160.0 x 36.8 x 2.00

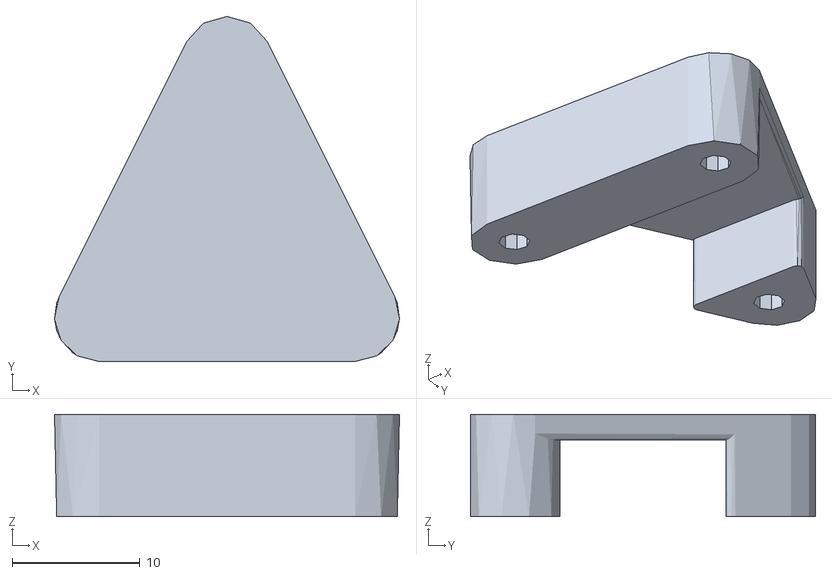
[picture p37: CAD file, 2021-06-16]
3Dprints/Halterung_Motorcontroller.stl
27.0 x 27.0 x 8.00

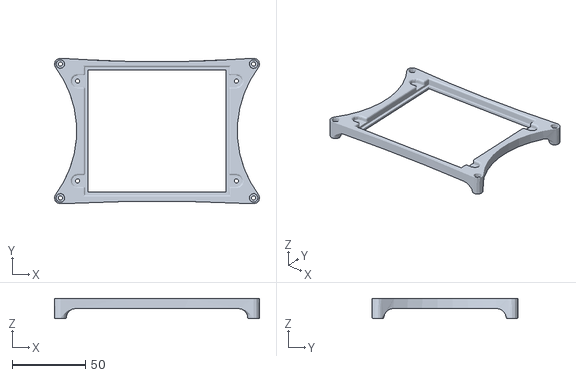
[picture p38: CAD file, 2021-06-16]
3Dprints/Halterung Display_Platine.stl
140.1 x 99.4 x 14.0

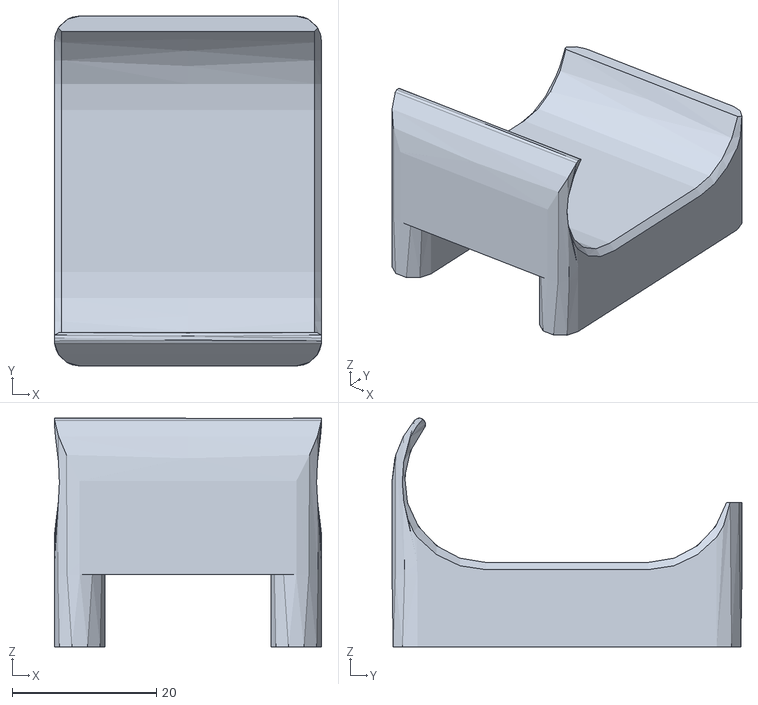
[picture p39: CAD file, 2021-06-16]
3Dprints/Halterung_Akku.stl
37.0 x 48.5 x 31.7

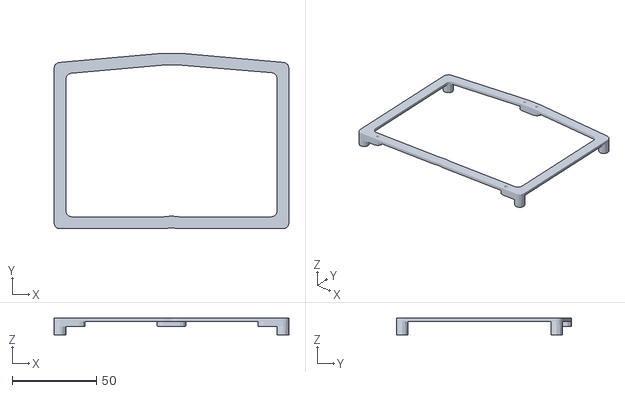
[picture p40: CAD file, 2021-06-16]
3Dprints/Halterung_Controller.stl
139.1 x 103.8 x 10.0

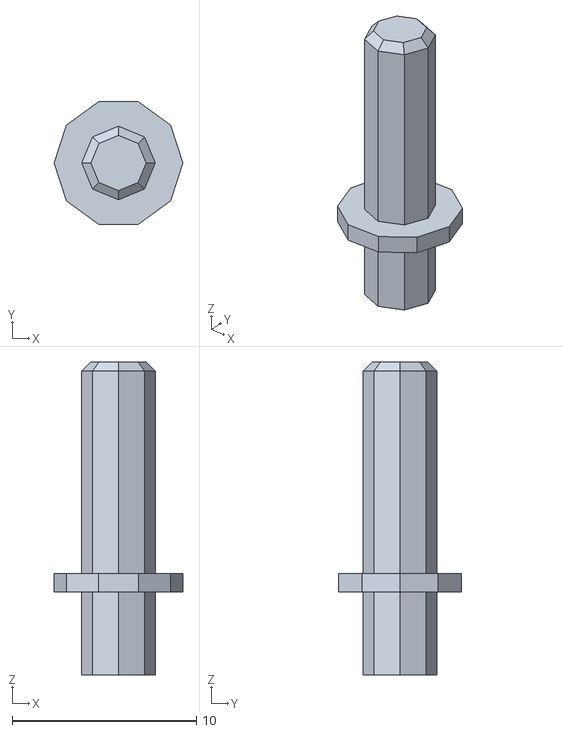
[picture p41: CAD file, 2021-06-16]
3Dprints/Display_Button.stl
7.00 x 6.66 x 17.0

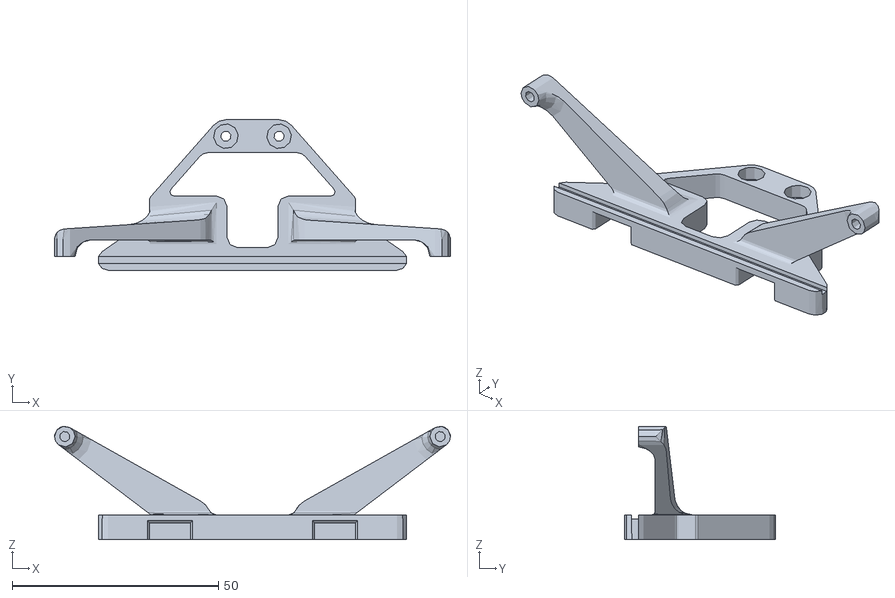
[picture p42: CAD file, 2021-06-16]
3Dprints/Halterung_Ultraschallboard.stl
96.0 x 36.5 x 27.5

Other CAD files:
3Dprints/Seitenschweller_rechts.stl
3Dprints/Stoßstange.stl
3Dprints/Antriebsabdeckung/Antriebsabdeckung v4.f3d

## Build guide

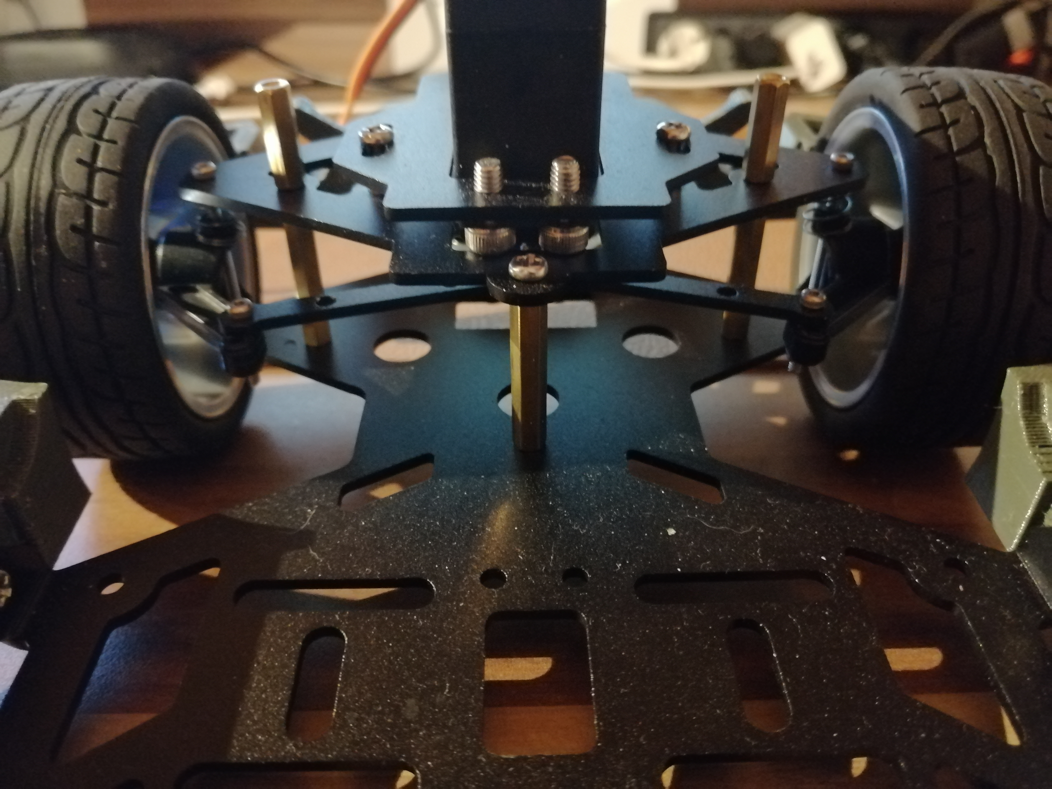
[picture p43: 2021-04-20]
pictures/06_Assembly/(6).jpg

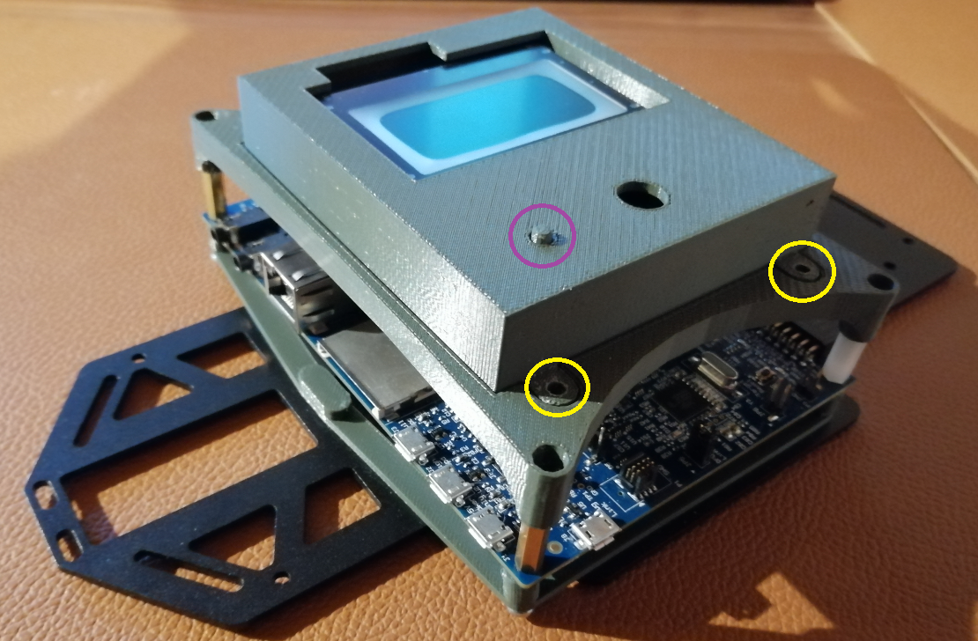
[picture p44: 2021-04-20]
report/sec2/images/3DAnbaukomponenten/Montagebilder/AbdeckungMontage.png

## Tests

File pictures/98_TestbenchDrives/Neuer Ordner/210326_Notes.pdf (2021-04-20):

Notizen NXP Cup 26.03.21

- BLDC Strangspannung gemessen (Ground von ESC und Phase schwarz von BLDC)
- Zwei Messungen mit ESC als Ansteuerung (schnell und langsam)
- Zwei Messungen mit DC Motor als Antrieb der Reifen (schnell und langsam)
- 20 Messungen Drehzahlabhängigkeit (Versorgungsspannung und Spannung an DC Motoren
- MCU Bezeichnung ist irgendwo falsch (muss LPC54628 sein; Kapitel 3)

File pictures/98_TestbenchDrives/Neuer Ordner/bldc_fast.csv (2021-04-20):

x-axis | 1
second | Volt
-4.200000E-03 | -738.316581E-03
-4.195800E-03 | -793.991999E-03
-4.191600E-03 | +2.688020988E+00
-4.187400E-03 | +2.879773833E+00
-4.183200E-03 | +2.879773833E+00
-4.179000E-03 | +2.916944895E+00
-4.174800E-03 | +2.972620312E+00
-4.170600E-03 | +3.052859972E+00
-4.166400E-03 | -738.316581E-03
-4.162200E-03 | -596.179268E-03
-4.158000E-03 | -571.452677E-03
-4.153800E-03 | +4.188334980E+00
-4.149600E-03 | +3.362185888E+00
-4.145400E-03 | +3.362348237E+00
-4.141200E-03 | +3.467152139E+00
-4.137000E-03 | +3.491878730E+00
-4.132800E-03 | +3.522989906E+00
-4.128600E-03 | +3.585049909E+00
-4.124400E-03 | -175.502516E-03
-4.120200E-03 | -175.502516E-03
-4.116000E-03 | -26.818269E-03
-4.111800E-03 | +5.670416359E+00
-4.107600E-03 | +3.825768888E+00
-4.103400E-03 | +4.005401962E+00
-4.099200E-03 | +4.005401962E+00
-4.095000E-03 | +4.030453252E+00
-4.090800E-03 | +4.085479272E+00
-4.086600E-03 | +3.981000069E+00
-4.082400E-03 | +195.234004E-03
-4.078200E-03 | +226.507530E-03
-4.074000E-03 | +288.729882E-03
-4.069800E-03 | +4.836096838E+00
-4.065600E-03 | +4.420181177E+00
-4.061400E-03 | +4.487814017E+00
-4.057200E-03 | +4.487814017E+00
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

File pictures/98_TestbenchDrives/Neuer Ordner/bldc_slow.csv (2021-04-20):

x-axis | 1
second | Volt
-4.400000E-03 | -14.698498E-03
-4.395600E-03 | -95.100507E-03
-4.391200E-03 | -95.100507E-03
-4.386800E-03 | -72.145426E-03
-4.382400E-03 | -37.693062E-03
-4.378000E-03 | -164.044717E-03
-4.373600E-03 | -49.190344E-03
-4.369200E-03 | -175.463033E-03
-4.364800E-03 | -141.089636E-03
-4.360400E-03 | -163.965751E-03
-4.356000E-03 | -95.100507E-03
-4.351600E-03 | -118.134555E-03
-4.347200E-03 | -95.100507E-03
-4.342800E-03 | -95.100507E-03
-4.338400E-03 | -95.179473E-03
-4.334000E-03 | -95.100507E-03
-4.329600E-03 | -106.676755E-03
-4.325200E-03 | -37.574613E-03
-4.320800E-03 | -95.100507E-03
-4.316400E-03 | -26.077331E-03
-4.312000E-03 | -14.698498E-03
-4.307600E-03 | -95.218956E-03
-4.303200E-03 | -141.168602E-03
-4.298800E-03 | -106.716238E-03
-4.294400E-03 | -95.100507E-03
-4.290000E-03 | -118.213521E-03
-4.285600E-03 | -106.439857E-03
-4.281200E-03 | -95.100507E-03
-4.276800E-03 | -95.100507E-03
-4.272400E-03 | -141.208085E-03
-4.268000E-03 | -175.502516E-03
-4.263600E-03 | -95.100507E-03
-4.259200E-03 | -152.350020E-03
-4.254800E-03 | -95.100507E-03
-4.250400E-03 | -140.852738E-03
-4.246000E-03 | -175.305101E-03
-4.241600E-03 | -129.355455E-03
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

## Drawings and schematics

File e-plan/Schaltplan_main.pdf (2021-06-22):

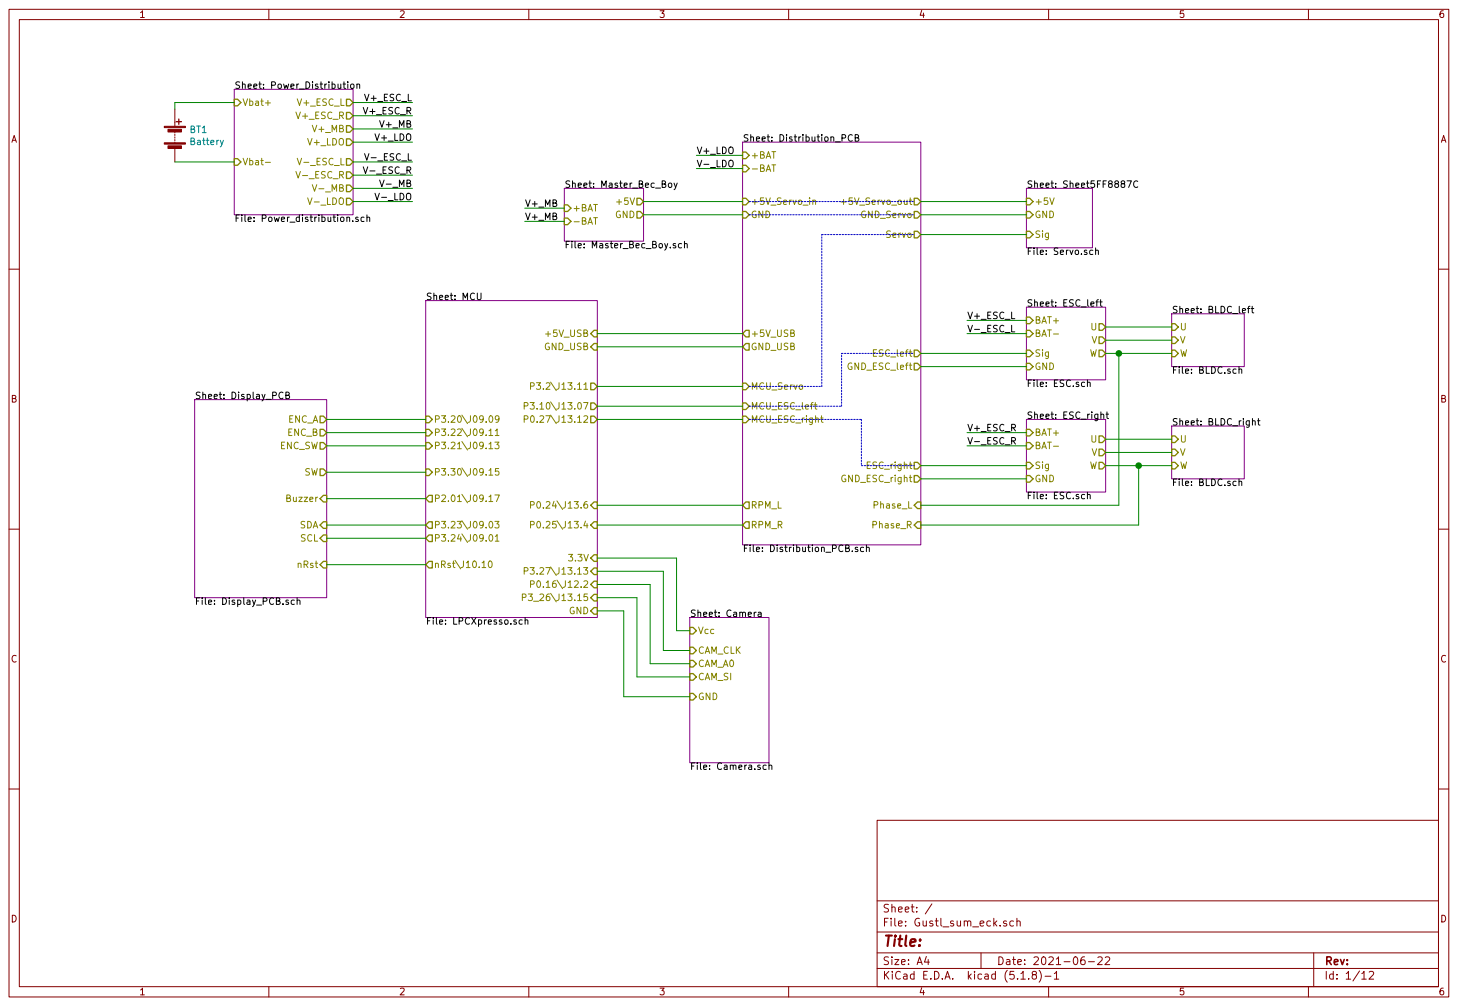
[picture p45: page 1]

Sheet: BLDC_left File: BLDC.sch U

Sheet: BLDC_right File: BLDC.sch U

Phase_L Phase_R
Sheet: Camera File: Camera.sch GND
CAM_SI CAM_A0 Vcc CAM_CLK

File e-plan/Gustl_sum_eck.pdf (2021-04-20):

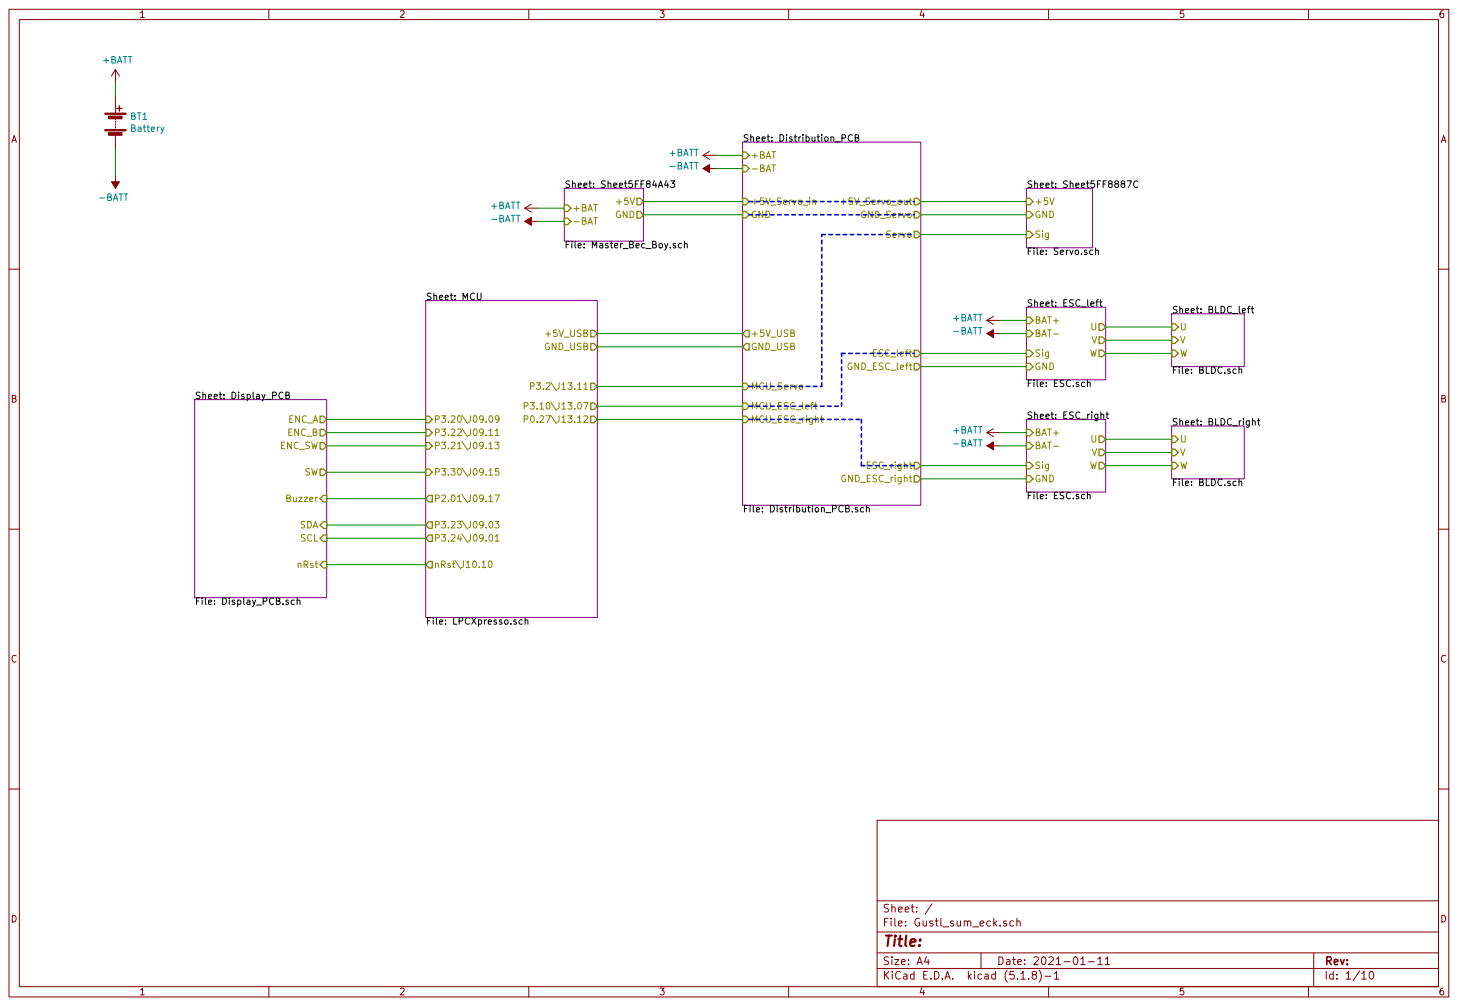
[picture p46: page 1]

Sheet: Sheet5FF84A43 File: Master_Bec_Boy.sch +BAT

Sheet: BLDC_right File: BLDC.sch U

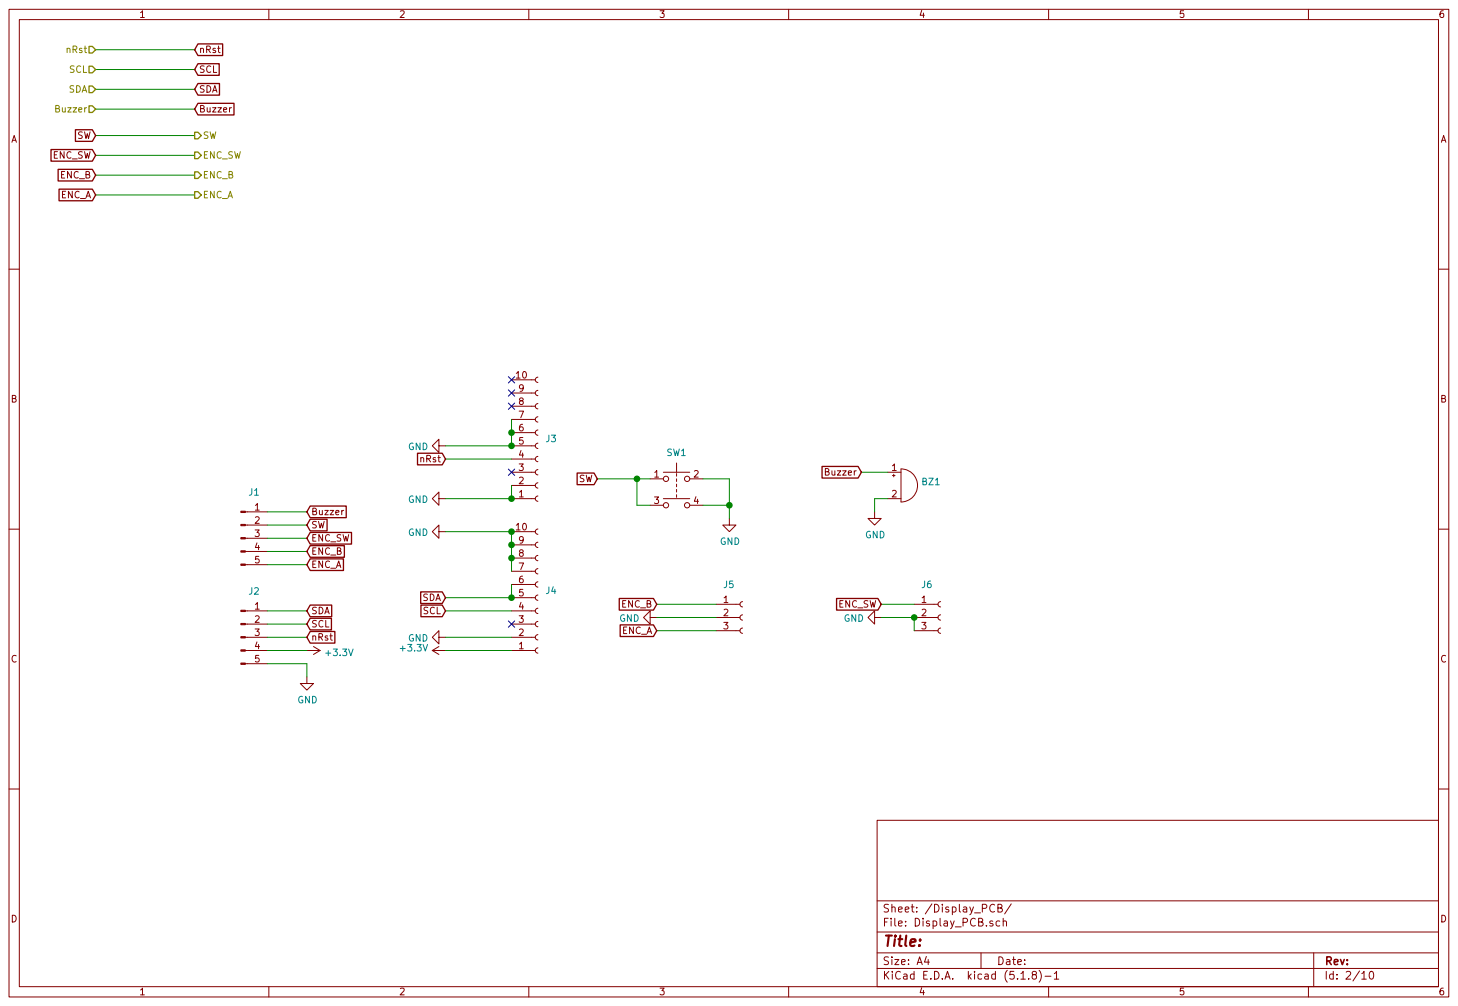
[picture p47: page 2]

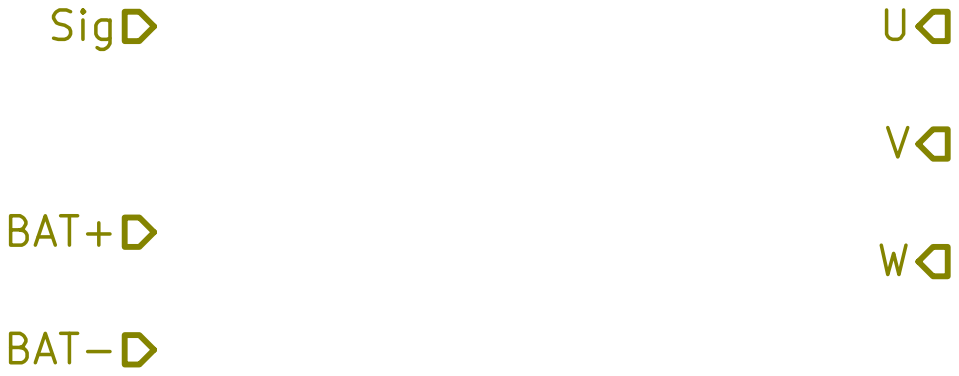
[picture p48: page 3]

Id: 3/10 Title: File: ESC.sch Sheet: /ESC_left/

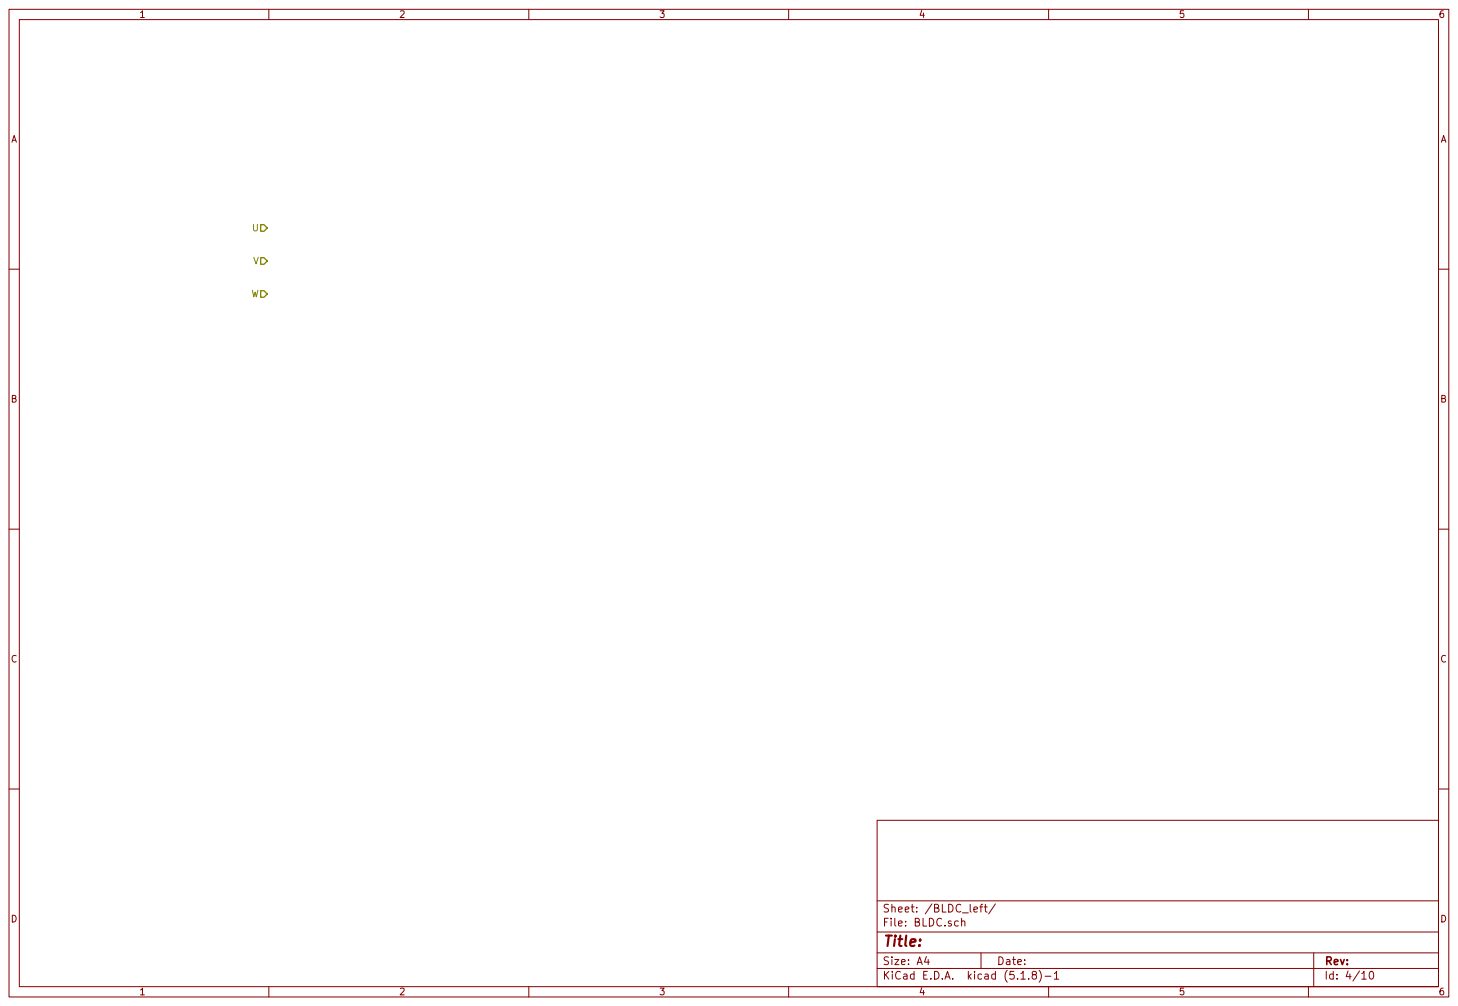
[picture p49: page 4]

Id: 4/10 Title: File: BLDC.sch Sheet: /BLDC_left/

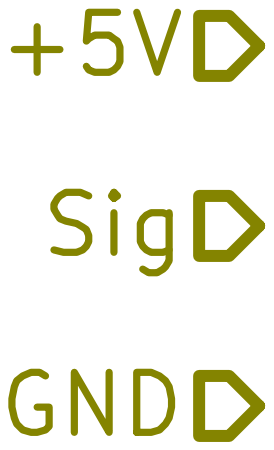
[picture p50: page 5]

Id: 5/10 Title: File: Servo.sch Sheet: /Sheet5FF8887C/

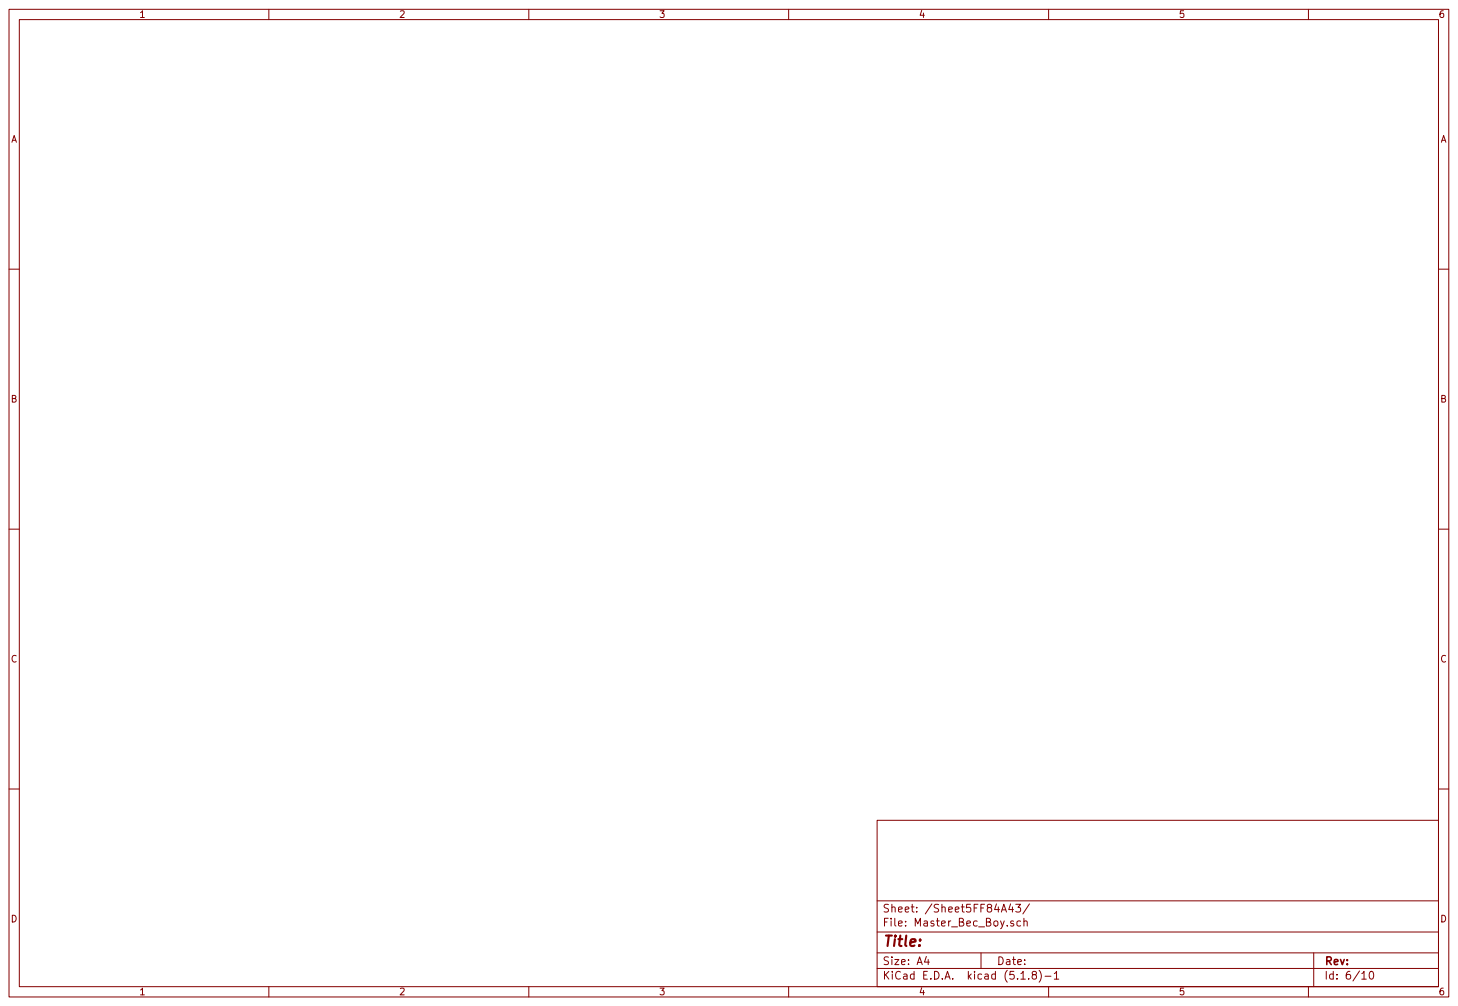
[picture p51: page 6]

Id: 7/10 Title: File: ESC.sch Sheet: /ESC_right/

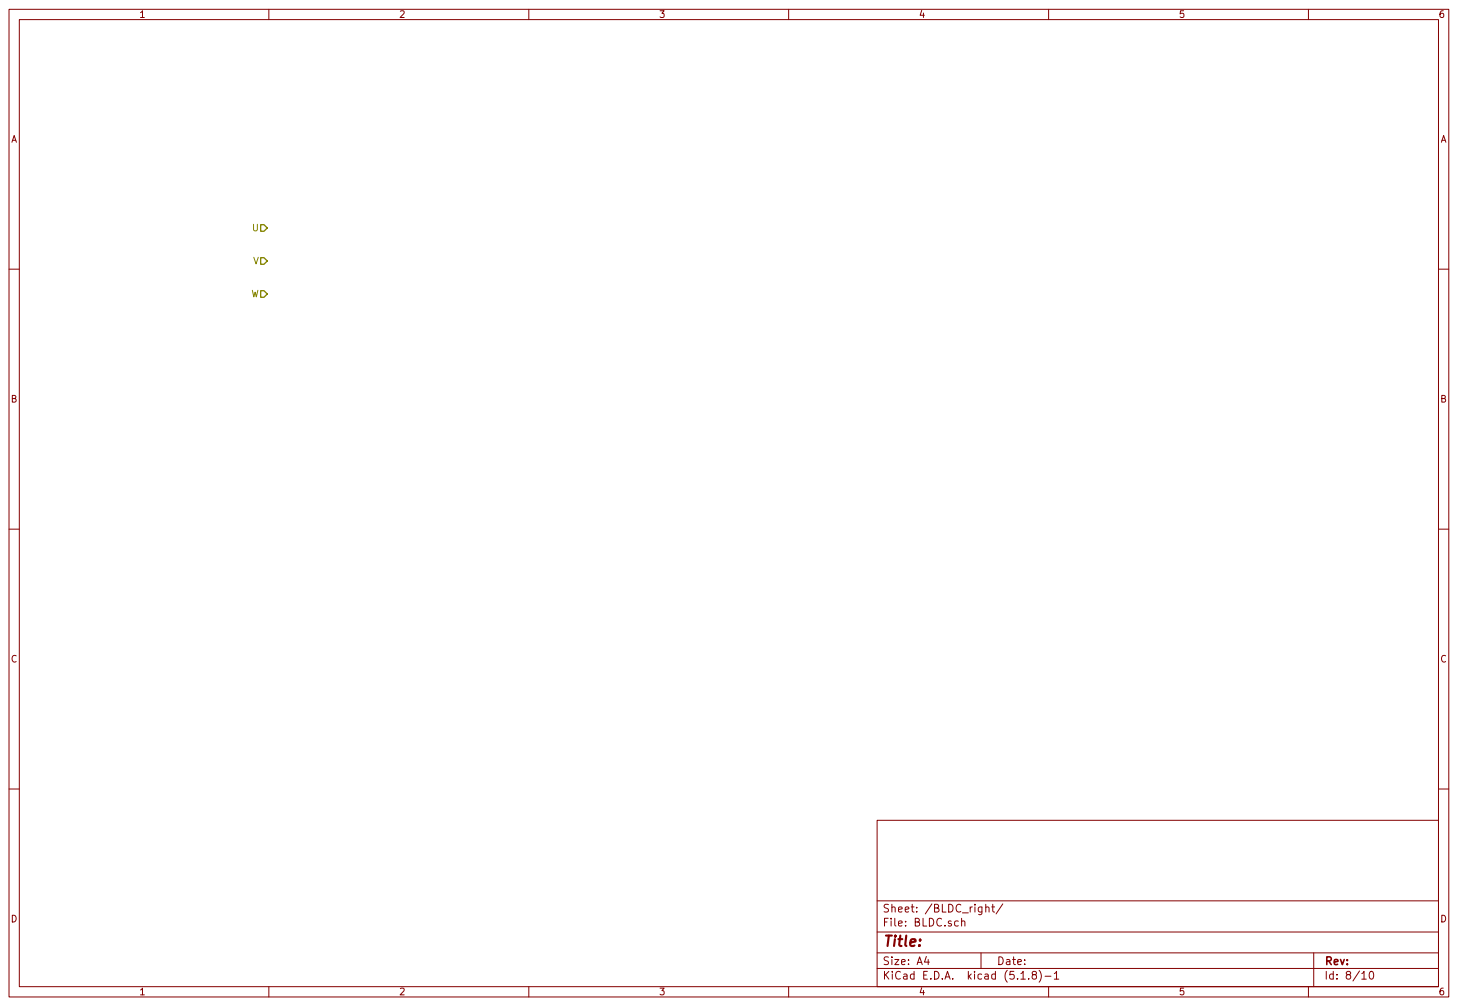
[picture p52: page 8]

Id: 8/10 Title: File: BLDC.sch Sheet: /BLDC_right/

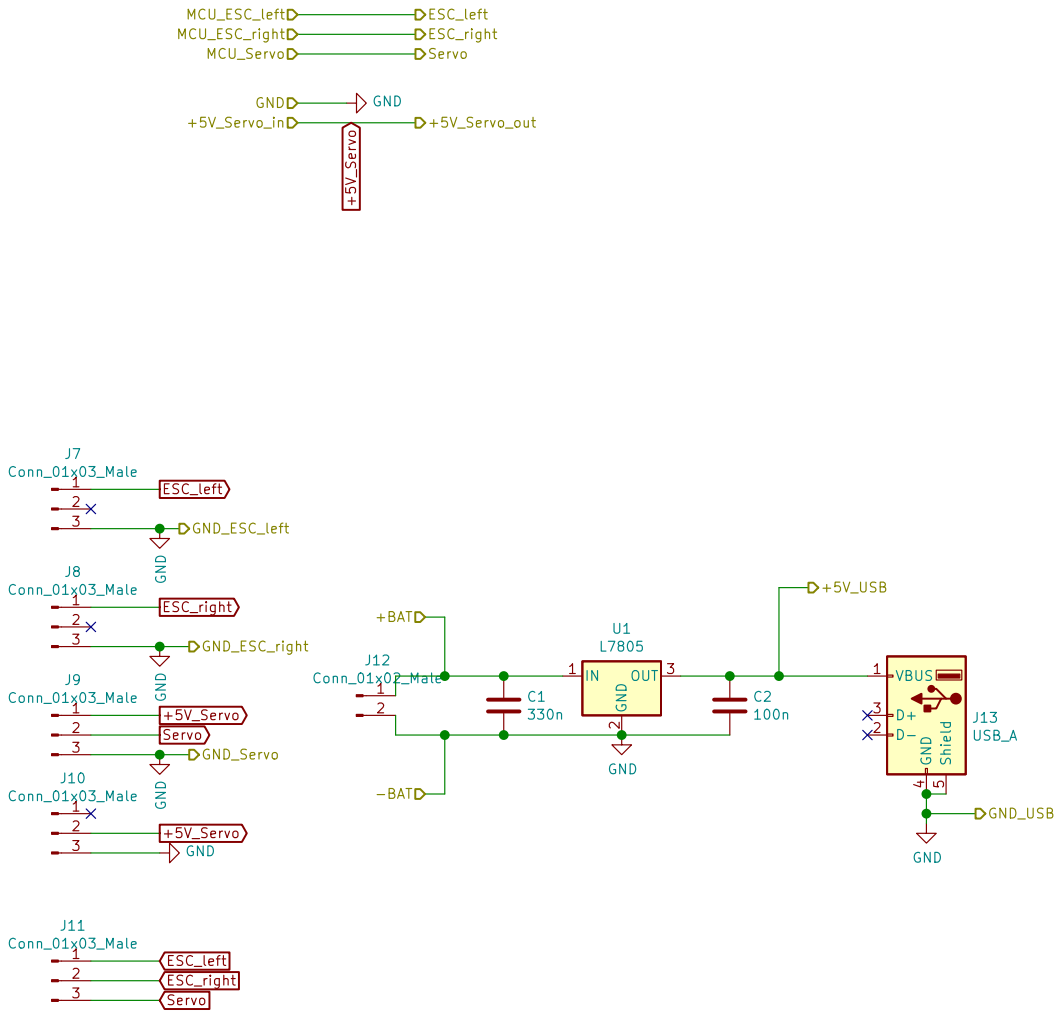
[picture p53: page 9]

J13 USB_A GND GND GND GND

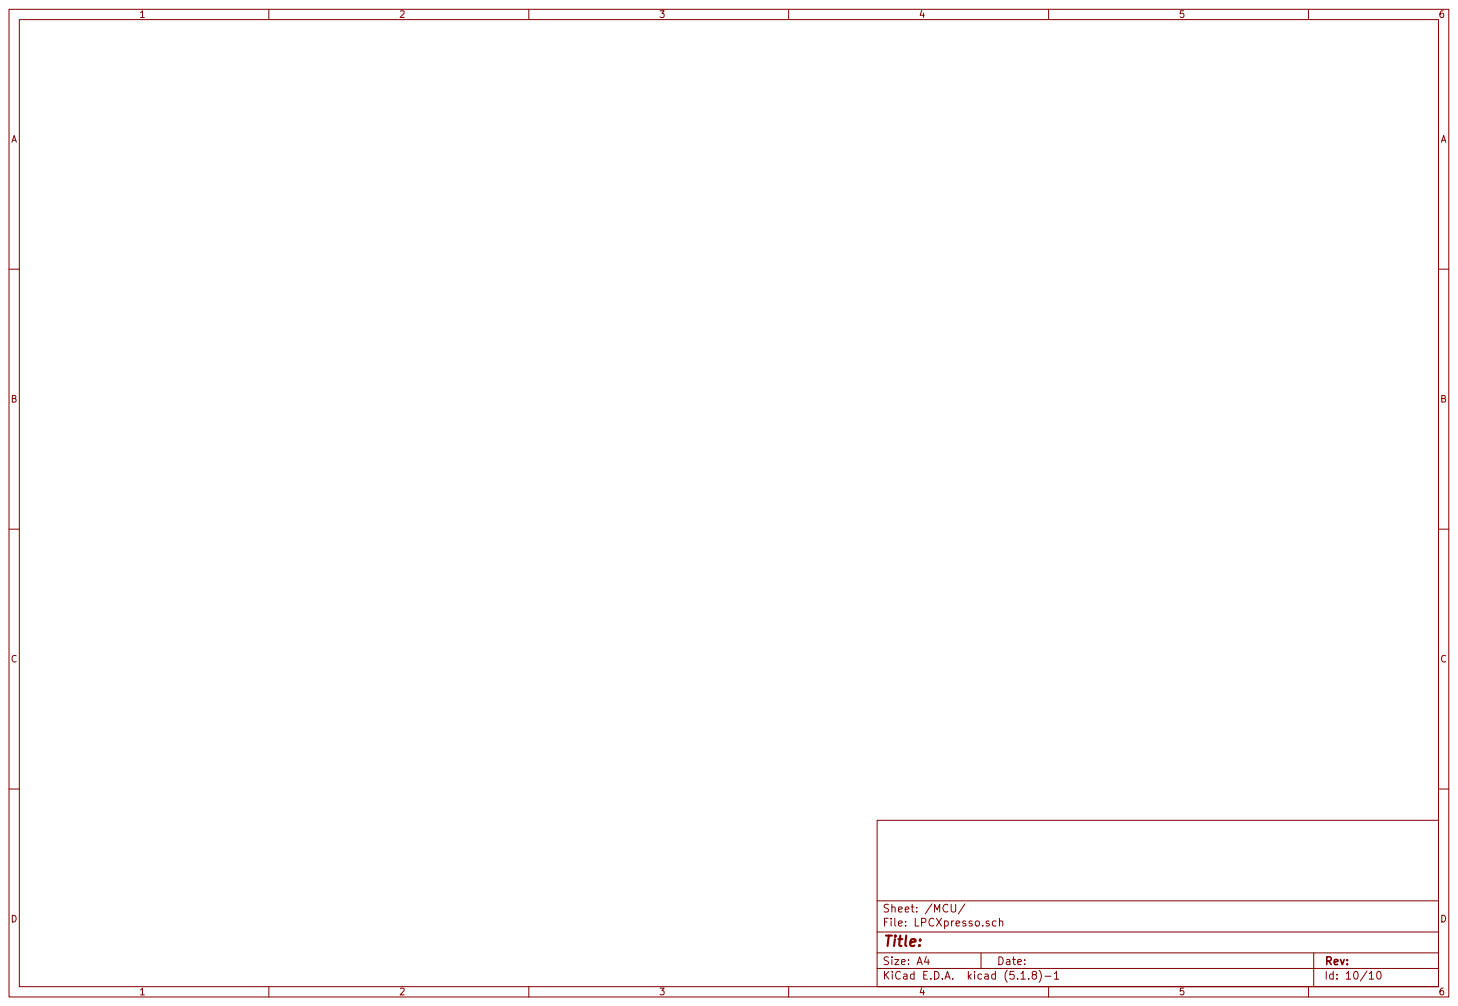
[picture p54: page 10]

File: LPCXpresso.sch Sheet: /MCU/
Id: 10/10 Title:

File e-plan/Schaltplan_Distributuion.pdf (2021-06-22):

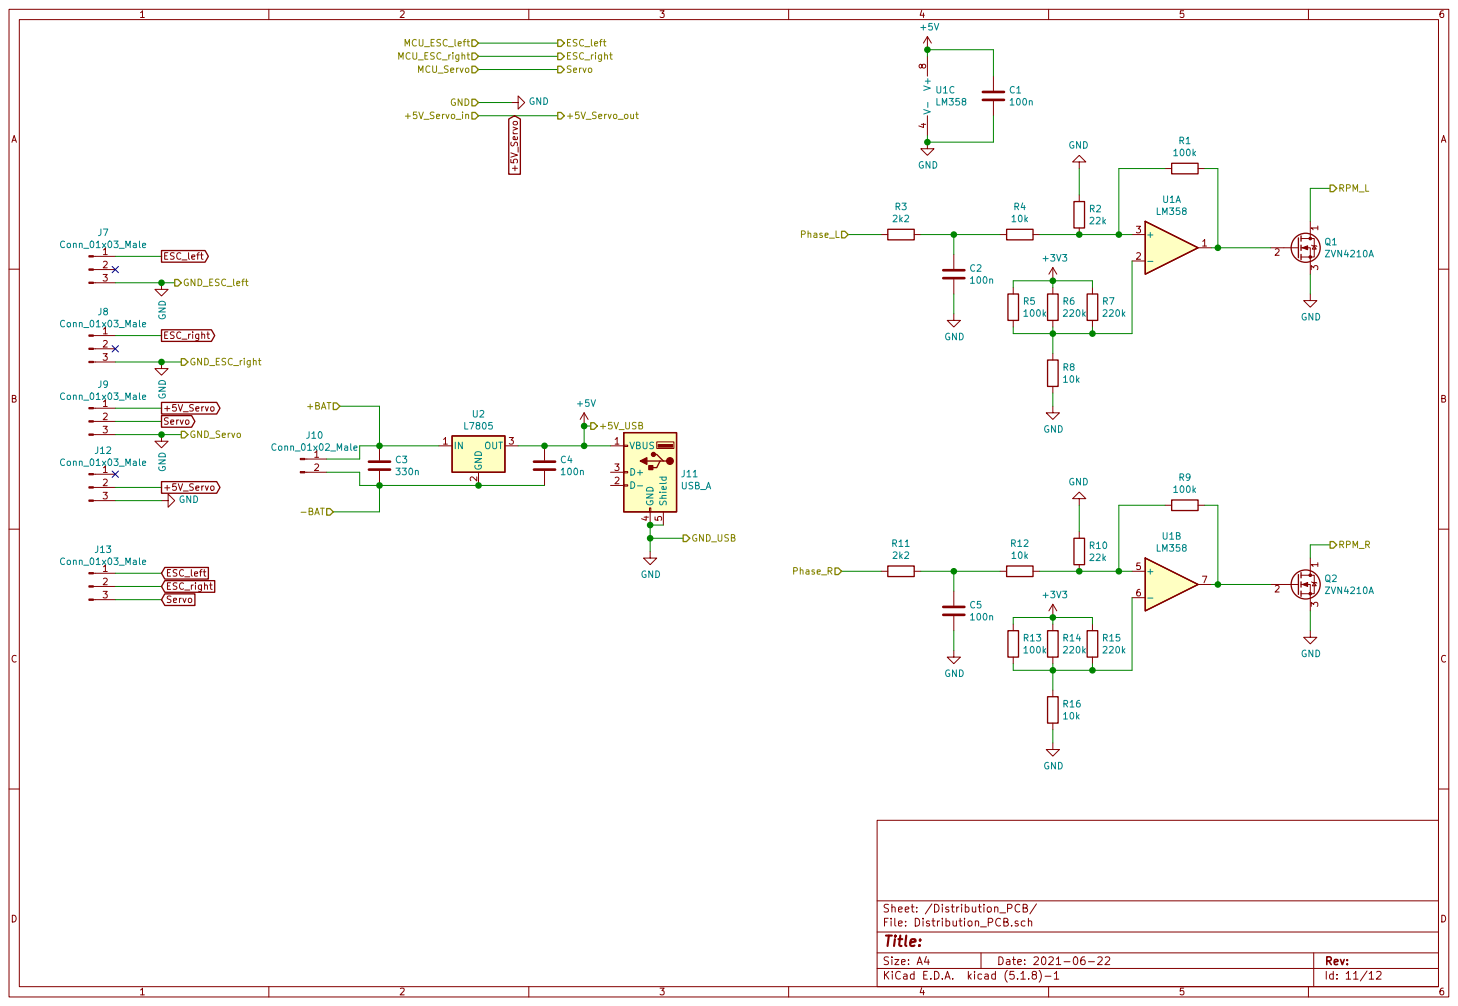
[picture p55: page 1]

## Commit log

2021-04-20 Pictures and Eplan added
    [mclk220.csv]
2021-04-20 added e-components and e-plan
    [e-components.xlsx, pin-assignment.xlsx]
2021-04-20 added Camera_operating-manual-28317.pdf
2021-04-20 Added testbench pictures
    [bldc_fast.csv, bldc_slow.csv, dc_fast.csv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]
2021-04-20 moved pin assignment
2021-06-16 Updated Documentation
    [Bodenteil_Stoßstange.stl, Deckel_Display.stl, Display_Button.stl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]
2021-06-19 Kamera Kapitel fertig geschrieben und Verteilerplatinen Kapitel fertig geschrieben
2021-06-21 Bericht fertig gemacht
    [2021-04-26_Bestellung_Conrad_NXP-Cup.xlsx, Antriebsabdeckung v4.f3d, Antriebsabdeckung v4.stl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]
2021-06-22 fertig gestellt
    [5VRegulator.sch, BLDC.sch, BLDC_left.sch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]
